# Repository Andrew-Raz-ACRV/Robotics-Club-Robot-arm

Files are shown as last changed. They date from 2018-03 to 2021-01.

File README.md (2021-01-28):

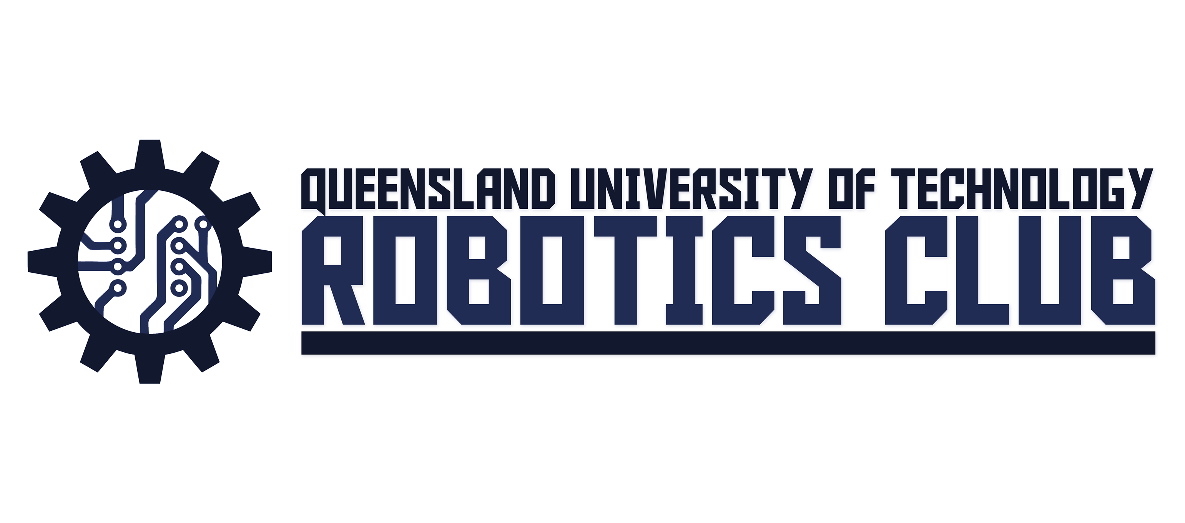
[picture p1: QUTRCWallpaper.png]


# Robotics-Club-Robot-arm
This project is part of the 2018 workshop series for the QUT Robotics club. It is based on the unit called Introduction to Robotics which is a subject focussed on the control of a Robotic arm and the application of computer vision processes. For half the project, the focus was on developing our own brand of robotic arms (Armageddon) with a position-based inverse kinematics controller that made the toolpoint of the robot follow a trajectory given by keyboard presses. The second half expanded the work towards an autonomous picking system where the robot uses a camera to see a ball, given some reference points to its frame of reference, and plan a trajectory to pick up the ball and place it into a box. There is also additional code to teleoperate the arm using a USB gamepad.

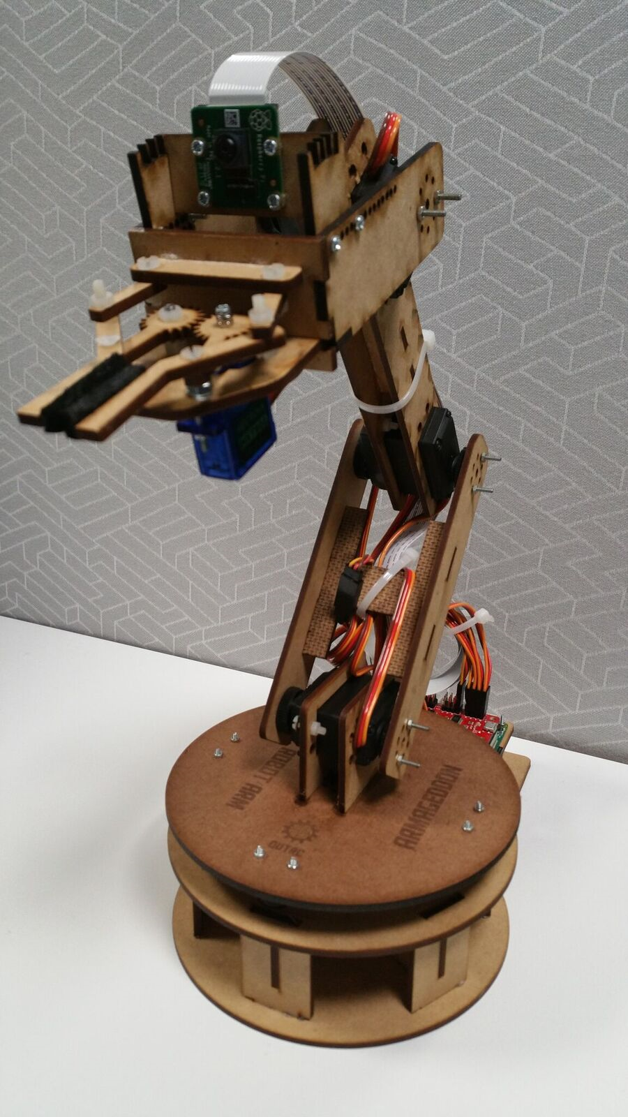
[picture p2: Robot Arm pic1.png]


## Getting Started with the Project
This project is based on using the robotic arms designed by the club which involve components:
* Raspberry Pi 3 B+ with a NOOBS sd card
* Raspberry Pi Camera
* Power adapter for the Raspberry Pi
* Sparkfun Raspberry Pi Servo hat
* Hobby King servos
* Laser cut parts developed by the club which is on this Github
a more comprehensive parts list is in this Github as well.

### Prerequisites
The Raspberry Pi project requires a few installations
- Getch is for capturing keyboard presses: https://pypi.org/project/getch/
- smbus for the i2c communication to the servo hat: https://learn.sparkfun.com/tutorials/pi-servo-hat-hookup-guide/all#software---python
- An old version of opencv that can be installed easily and quickly 
- Optional installation with matlibplot
- Note: you will need to enable i2c and the camera in pi configurations

Installations for the Kinematics Half of the Project:
```
sudo apt-get install getch
sudo apt-get install smbus
```

Installations for the Computer Vision half of the project:
```
sudo apt-get install python opencv
sudo apt-get install python matlibplot
```
USB Gamepad Teleoperation installation:
```
sudo pip install evdev
```
## Running Robot Arm Tests:

Robot Arm Calibration Test:
In Robot Arm control Workshops, you can test the calibration of the servos to see if they are accurate
```
python3 calibration.py
```

Computer Vision Threshold Test:
In Computer_vision_Workshops, you can run a script to see the thresholding
```
python test_video_blobdetection.py
```

In Gamepad demo Test:
Use the first line of code to determine which event the gamepad is (event3 by default)
```
ls /dev/input
python gamepad_demo.py
```
## Contents on this Github:
This Github holds the following:
* Laser cut file (CorelDraw) of the Robot Arm
* Parts List for Constructing the Robot Arm
* MATLAB simulation of the inverse Kinematics provided with Andrew's Kinematics functions
  Run the file RobotArmSimulator.m
* Workshop Slides with Theory explained in them
* Python scripts of the Workshop tasks
* Python scripts of the Final Demo Scripts

## Final Demo Scripts:

In the Terminal, you can run these commands to run the demos:

The Robot Arm Teleoperation Script in Python 3
In Teleoperation_Demo_Python3:
```
python3 RobotArmRaspberryPi_Complete_Code.py
```

The Robotic Vision Autonomous Picking Script in Python 2
In VisionArm_Demo_Python2:
```
python VisionArm.py
```

USB Gamepad teleoperation demo of Robot arm in Python 2
```
python RobotArm_Gamepad_teleop.py
```

## Author

* **Andrew Razjigaev** - *President of the QUT Robotics Club 2018*  

## Acknowledgments
* Student Clubs and Projects (SCAP) Fund 2018
* Krishan Rana - For his Development of the gripper and Laser cut pieces for the joints.
* Marty - For his assistance with running the Computer Vision task

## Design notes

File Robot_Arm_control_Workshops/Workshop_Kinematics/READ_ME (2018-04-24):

Today's Workshop you need to complete a few functions:
In the Utilities module complete:

-Initialise_Robot_arm
-move_arm_deg
-move_arm_rad

In the Kinematics Module Complete:
-ForwardKinematics
Fill in the DH parameters

*You'll need to read the Kinematics document in internet 
Chromium to understand what to fill in ForwardKinematics
Otherwise, just ask and I'll be happy to explain.

After that you can control the arm to go to any 
motor angle you like just for fun in Robot_script.py

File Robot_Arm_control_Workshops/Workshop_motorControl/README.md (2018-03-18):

- Software - Python -
We’ll go over in some detail here how to access and use the pi servo hat in Python.

References: https://learn.sparkfun.com/tutorials/pi-servo-hat-hookup-guide#software---python

- Set Up Access to SMBus Resources - 

First point: in most OS level interactions, the I2C bus is referred to as SMBus. 
If doing this for the first time, you'll need to go to the pi-config settings and enable i2c communication.
Do this by going to the terminal or using the start menu option:

sudo raspi-config

From the window that appears, navigate to 'Interfacing options' which leads to the option of enabling i2c.
The change requires rebooting. Afterwards, you can get the SMBus module by typing this in the terminal:

sudo apt-get install python3-smbus i2c-tools

You can also type in this command to find the part's address which is 0x40 by default:
i2cdetect –y 1 

- Using the SMBus Resources for Motor Control -

Open a python3 script and start typing this code:

import smbus
bus = smbus.SMBus(1)

This imports the smbus module, creates an object of type SMBus, and attaches it to bus “1” of the Pi’s various SMBuses.
We have to tell the program the part’s address. By default, it is 0x40, so set a variable to that for later use.

addr = 0x40

Next, we want to enable the PWM chip and tell it to automatically increment addresses after a write (that lets us do single-operation multi-byte writes).

bus.write_byte_data(addr, 0, 0x20)
bus.write_byte_data(addr, 0xfe, 0x1e)

- Write Values to the PWM Registers to Control Servos -

That’s all the setup that needs to be done. From here on out, we can write data to the PWM chip and expect to have it respond. Here’s an example.

bus.write_word_data(addr, 0x06, 0)
bus.write_word_data(addr, 0x08, 1250)

The first write is to the “start time” register for channel 0. By default, the PWM frequency of the chip is 200Hz, or one pulse every 5ms. The start time register determines when the pulse goes high in the 5ms cycle. All channels are synchronized to that cycle. Generally, this should be written to 0. The second write is to the “stop time” register, and it controls when the pulse should go low. The range for this value is from 0 to 4095, and each count represents one slice of that 5ms period (5ms/4095), or about 1.2us. Thus, the value of 1250 written above represents about 1.5ms of high time per 5ms period.

Servo motors get their control signal from that pulse width. Generally speaking, a pulse width of 1.5ms yields a “neutral” position, halfway between the extremes of the motor’s range. 1.0ms yields approximately 90 degrees off center, and 2.0ms yields -90 degrees off center. In practice, those values may be slightly more or less than 90 degrees, and the motor may be capable of slightly more or less than 90 degrees of motion in either direction.

To address other channels, simply increase the address of the two registers above by 4. Thus, start time for channel 1 is 0x0A, for channel 2 is 0x0E, channel 3 is 0x12, etc. and stop time address for channel 1 is 0x0C, for channel 2 is 0x10, channel 3 is 0x14, etc. See the table below.

Channel #
Start Address
Stop Address

Ch 0
0x06
0x08

Ch 1
0x0A
0x0C

Ch 2
0x0E
0x10

Ch 3
0x12
0x14

Ch 4
0x16
0x18

Ch 5
0x1A
0x1C

Ch 6
0x1E
0x20

Ch 7
0x22
0x24

Ch 8
0x26
0x28

Ch 9
0x2A
0x2C

Ch 10
0x2E
0x30

Ch 11
0x32
0x34

Ch 12
0x36
0x38

Ch 13
0x3A
0x3C

Ch 14
0x3E
0x40

Ch 15
0x42
0x44

If you write a 0 to the start address, every degree of offset from 90 degrees requires 4.6 counts written to the stop address. In other words, multiply the number of degrees offset from neutral you wish to achieve by 4.6, then either add or subtract that result from 1250, depending on the direction of motion you wish. For example, a 45 degree offset from center would be 207 (45x4.6) counts either more or less than 1250, depending upon the direction you desire the motion to be in.

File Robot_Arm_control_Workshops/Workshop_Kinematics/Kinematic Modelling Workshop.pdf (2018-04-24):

KINEMATIC MODELLING WORKSHOP The next two sections refer to Peter Corke’s Textbook [1]. His content is also available as

videos in the Robot Academy website: https://robotacademy.net.au/

Understanding 3D space using Homogeneous Transforms
In robotics, we tend represent the world as a 3D Cartesian space where points are coordinate vectors with components on each axis:

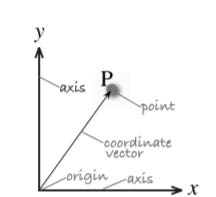
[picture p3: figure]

# PPAA = [TTxx TTyy TTzz]

Each point in space is measured from a Cartesian coordinate frame and has a letter on top that tells you what frame it’s measured from.
A similar set-up is done when you have multiple coordinate frames. A transform from one frame to another is represented as a pose (position and orientation). The letter at the top left of it tells you the frame it’s measuring from and the bottom right letter tells you where the transform goes to:

ξξBB

# AA = tttttttttttttttttt ff AA tttt ff BB

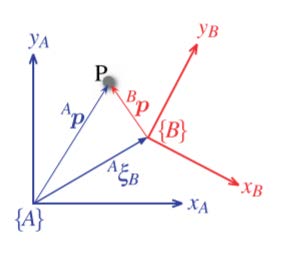
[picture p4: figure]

This is useful when you want to find where one measured point is to another frame e.g.:

# PPAA = ξξBB

# AA PPBB

This means that the transform from frame A to B of the point measured in frame B becomes the same point measured in frame A. This transform can be cascaded to transform from many more coordinate frames:

# PPAA = ξξBB

# AA ξξCC

# BB PPCC

For the robot arm project we’ll use this theory to find where the gripper is from the base:

# PPGGGGGGGGGGGGGG

# BBBBBB = ξξJJJJ JJJJ1

BBBBBB | ξξJJJJ JJJJ2 JJJJ JJJJ1 | ξξJJJJ JJJJ3 JJJJ JJJJ2 | PPGGGGGGGGGGGGGG JJJJ JJJJ3

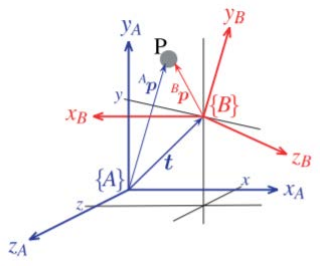
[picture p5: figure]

We can represent the transform as a matrix, like so:
ξξBB

# AA → TTBB

AA =

# | TTxx … RRBB

# AA … TTyy

# | TTzz

0 0 0 1

The matrix is 4 by 4 with the top left 3 by 3 being a 3D rotation Matrix and the forth column having the translational components tt = [TTxx TTyy TTzz] of the transform in each axis. The bottom row is what makes it possible to

use the transforms in this way:

# TTGGGGGGGGGGGGGG

# BBBBBB = TTJJJJ JJJJ1

# BBBBBB × TTJJJJ JJJJ2 JJJJ JJJJ1 × TTJJJJ JJJJ3 JJJJ JJJJ2 × TTGGGGGGGGGGGGGG JJJJ JJJJ3

Where you can use matrix multiplication (dot product) to cascade the transforms. To understand the rotation matrix think of it as an array of
components of each axis. Note: every axis is a unit vector. Based
on the figure to the right, you’ll see that new axis is split into
components measured on the old axis:
RRBB

VV →

∗

# aa aa xxVV aa aa yyVV aa aa zzVV

# xxBB yyBB zzBB

# cos θθ − sin θθ 0 sin θθ cos θθ 0

0 0 1

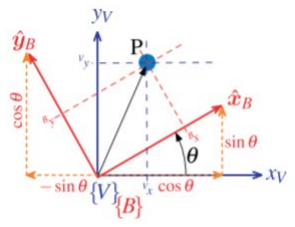
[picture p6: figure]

The matrix means that for some x distance along xxBB is measured as that times cos θθ along

xxVV
And that for some y distance along yyBB is measured as that times − sin θθ along xxVV

And so on for each 3 components on each of the 3 axes … note that the z-axis in the figure is unchanged as theta rotates the frame about the z-axis, so therefore the z-axes components ‘resemble’ the identity matrix. A rotation matrix with no
rotation is an identity matrix. All rotation matrix components
must range between -1 and 1 and the determinant is always 1 to
be a valid rotation matrix. A point can be rotated using matrix multiplication like this:

# PPVV = RRBB

# VV PPBB

# PPVV =

# cos θθ − sin θθ 0 sin θθ cos θθ 0

0 0 1

TTXX
BB
TTYY
BB
TTZZ
BB

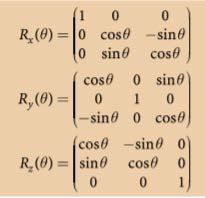
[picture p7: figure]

Rotation in 3D space means that a transform can not only translate in the x, y and z directions but rotate about the x, y and z axes. 3D rotation is commonly described by Euler angles roll pitch yaw. Rotation about the x-axis is roll, rotation about the y-axis is pitch and rotation about the z-axis is yaw.

# RR = RRXX(θθ rrrr) × RRYYθθ ppℎ × RRZZθθyy yy

Putting this together a transformation matrix is used like this:

Let’s say that RRBB

AA is z-axis rotation: RRZZ(θθ) and translation vector is tt = [5, 10, −5]

# PPAA = TTBB

# AA PPBB

# PPAA =

# cos θθ − sin θθ 0 5 sin θθ cos θθ 0 10

0 0 1 −5
0 0 0 1

TTXX
BB
TTYY
BB
TTZZ
BB
1

Which transforms the point PPBB to the same point but measured from the A frame

So overall, in 3D space, any object with a
coordinate frame can be represented as a
transform matrix from the world coordinate frame to it. The matrix consists of a 3 by 3 rotation matrix consisting of 3 parameters and a 3 by 1 translation vector consisting of 3 parameters. A transform is translation and rotation of an object in space based on 6 parameters: x, y, z, roll, pitch and yaw

DH Parameters in the Transform Matrix

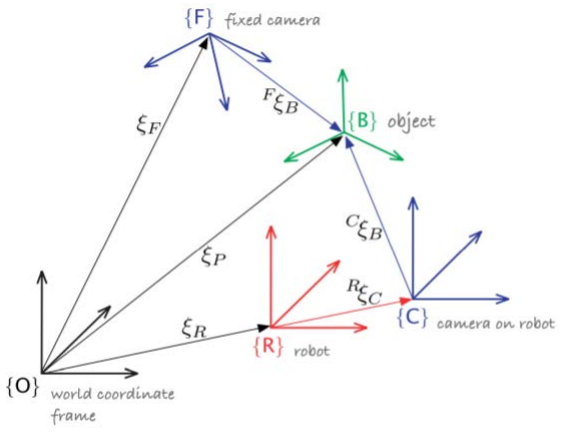
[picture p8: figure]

In the previous section, the transform from one coordinate frame to another in 3D space is described by 6 parameters. Denavit and Hartenburg said that for 3D transforms between revolute joints (ones that rotate only in one axis) can be simplified to only need 4 parameters.

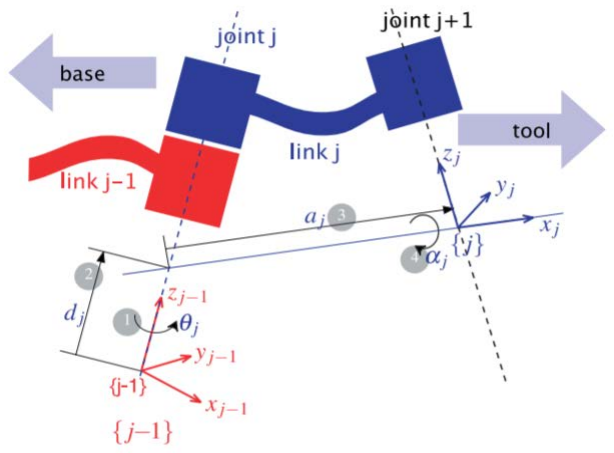
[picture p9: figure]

If you place the coordinate frames in a certain way (mainly placing the z axis as the axis of rotation and the x-axis as an axis to measure between axes), you can have the transform represented by only rotations and translations about the x and z axes:

So from frame j-1 to frame j, the transform is described by parameters θθ, dd, , αα

This yields a standard transformation matrix that we can plug and use for every joint:

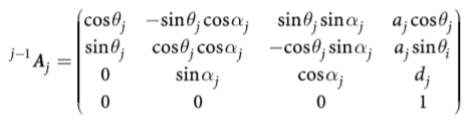
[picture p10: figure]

So every time you want to compute the transformation matrix among the joints, you need to find 4 parameters:

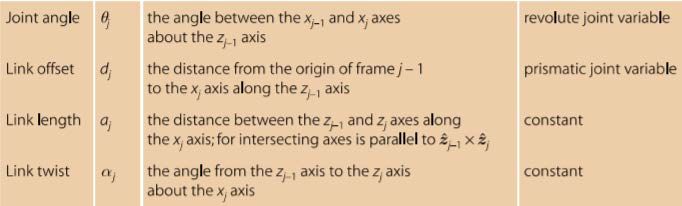
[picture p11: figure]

Solving the Forward Kinematics
Forward kinematics is the problem of finding out where the gripper is from the base of the robot. It can be represented as a function K of joint values to gripper pose:

# xx = KK(qq)

Where x is the tool point pose vector and q is the joint values vector of the robot arm Finding the pose of the gripper from the base can be solved using the transformation matrices learnt before:

# TTGGGGGGGGGGGGGG

# BBBBBB = TTJJJJ JJJJ1

# BBBBBB × TTJJJJ JJJJ2 JJJJ JJJJ1 × TTJJJJ JJJJ3 JJJJ JJJJ2 × TTGGGGGGGGGGGGGG JJJJ JJJJ3

Using the transform matrix TTGGGGGGGGGGGGGG BBBBBB we can extract the overall translation. The next

figure shows how the coordinate frames have been set to find the 4 DH parameters for each joint:

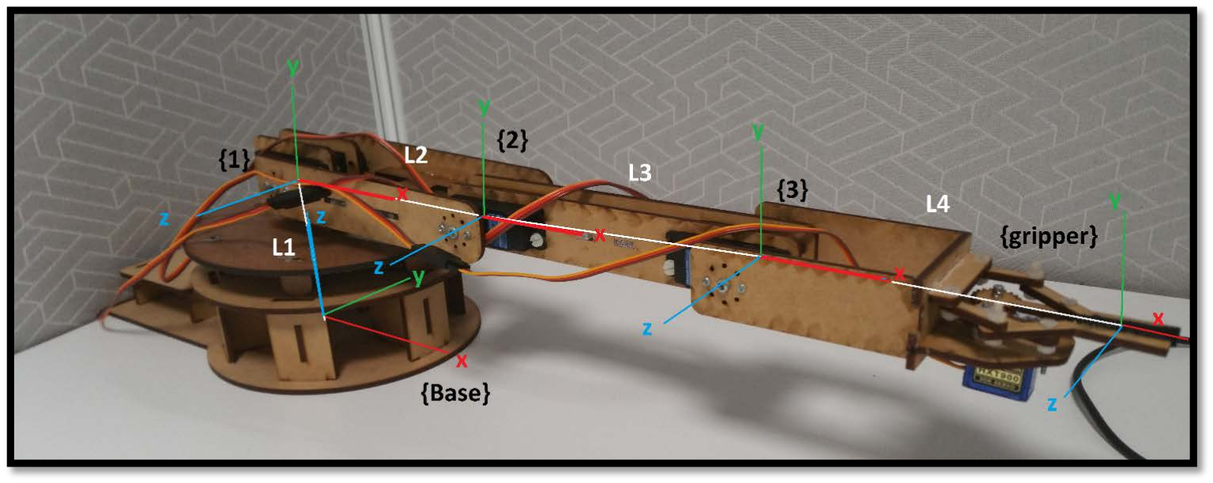
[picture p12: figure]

Note we will need the arm lengths:

# They are: LL1 = 100 , LL2 = 120 , LL3 = 140 , LL4 = 140

All translation is measured in mm
Each joint does a rotation in radians.
The variable angle produced by each joint is

# qq1, qq2, qq3, qq4

Computing the DH parameters yields:

DH Parameters | θθ | dd | aa | αα

# TTJJJJ JJJJ1 BBBBBB

# TTJJJJ JJJJ3 JJJJ JJJJ2

# TTJJJJ JJJJ2 JJJJ JJJJ1 TTGGGGGGGGGGGGGG JJJJ JJJJ3

We find the x, y, z coordinates by extracting the translation vector out of TTGGGGGGGGGGGGGG BBBBBB

The other value that is of interest to know is the pitch angle of the gripper. That value in intuitively going to be the sum of the joints:

# gg aaaa = θθPP = qq2 + qq3 + qq4

As we want to try controlling that angle and the position of the gripper

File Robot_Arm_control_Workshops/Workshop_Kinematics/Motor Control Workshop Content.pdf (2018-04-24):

# Motor Control Workshop Content:

### Low-Level Servo Control

Provided that i2c is enabled in PI-configuration, you may run code that uses the i2c communication which is the SMBus module. To control the servos first import that module and declare a bus connection.
- import smbus
- bus = smbus.SMBus(1)
Then provide the part address for the connection to go to which is 0x40 by default:
- addr = 0x40
Then initialize the settings for the communication by enabling the PWM chip and tell it to automatically increment addresses after a write (that lets us do single-operation multi-byte writes)
- bus.write_byte_data(addr, 0, 0x20)
- bus.write_byte_data(addr, 0xfe, 0x1e)
With this initialized, now the servos can be told to move to certain positions via Pulse Width Modulation (a method of changing the power delivered to a motor by changing the average voltage in the pulses). The yellow cable of the servo connector carries the control signal, used to tell the motor where to go. This control signal is a specific type of pulse train. Servo motors get their control signal from that pulse width. We can write commands to the servo that tell how big that pulse is, for example:
- bus.write_word_data(addr, 0x06, 0)
- bus.write_word_data(addr, 0x08, 1250)

The first write is to the “start time” register for channel 0 (indicated by using 0x06). By default, the PWM frequency of the chip is 200Hz, or one pulse every 5ms. The start time register determines when the pulse goes high in the 5ms cycle. All channels are synchronized to that cycle. Generally, this should be written to 0 i.e. the start of the period should be high. This only needs to be done once.
The second write is to the “stop time” register, and it controls when the pulse should go low (indicated by using 0x08 for channel 0). The range for this value is from 0 to 4095, and each count represents one slice of that 5ms period (5ms/4095), or about 1.2us. Thus, the value of 1250 written above represents about 1.5ms of high time per 5ms period.
Generally speaking, a pulse width of 1.5ms yields a “neutral” position, halfway between the extremes of the motor’s range. 1.0ms yields approximately 45 degrees off center, and 2.0ms yields -45 degrees off center. In practice, those values may be slightly more or less than 45 degrees, and the motor may be capable of slightly more or less than 45 degrees of motion in either direction.
Common servos rotate over a range of 90° as the pulses vary between 1 and 2ms – they should be at the center of their mechanical range when the pulse is 1.5ms: https://learn.sparkfun.com/tutorials/hobby-servo-tutorial#servo-motor-background

To achieve 1ms pulses, use a stop time of 836, likewise, to get 2ms pulses use a stop time of 1664.

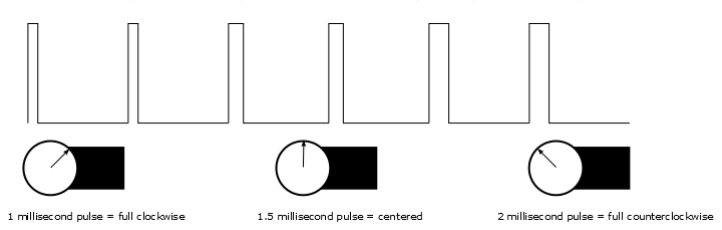
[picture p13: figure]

Using the module time to pause the code so that the servo has time to adjust to its position:
- time.sleep(2) # pause for two seconds
- bus.write_word_data(addr, 0x08, 836) # chl 0 end time = 1.0ms
- time.sleep(2)
- bus.write_word_data(addr, 0x08, 1664) # chl 0 end time = 2.0ms
Essentially, the servo position is controlled by the stop time of the pulse of the PWM which is a value that ranges from 0 (no power) to 4095 (Full power). Keeping it safe, the range used is from 836 to 1664 which allows a good 90 degrees of movement (acceptable for the arm to pick and place objects in its specific workspace).
See Appendix A for the start and stop addresses for using other channels on the PI hat.
For channel 0 in the example, the start address is 0x06 and the stop address is 0x08.

### High Level Control

The low level control showed that the position of the servo can by controlled by PWM pulses governed by integers from the range of 0 to 4095 with a mechanical working range of 836 to 1664. For the interest of understanding the kinematics of the arm, it is necessary to map that PWM to physical degrees or radians of rotation. For that, calibration is done where one should measure the angle output from each joint that undergoes the PWM values of 836, 1250 and 1664. The relationship is proportional and hence a linear relationship is required to map PWM to angle output. Using the calibration data, one can model the servo as a class object in python that has variables like joint limits and functions that can move the servo to a certain degrees or radians or read the current position of the joint. The functions for the PI servo class is in the Robotarm_ServoModule.py file in the workshop folder.

Measuring Convention of the Joints of the Arm:

To measure the joints consistently for each arm, the standard for placing the origin for the angles is proposed based on the right hand rule about the axis of rotation and the coordinate frames later on. To get the idea, the robot in the picture has the revolute base at 0, the next joint is at 135, the joint above that is at -100 and the joint above that one is at -90 degrees.

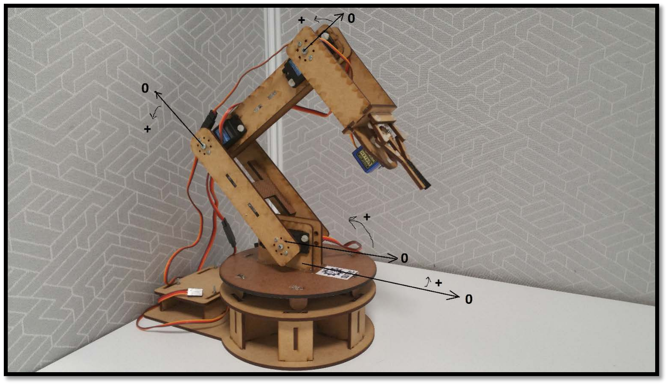
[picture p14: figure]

For the Robot arm, generally channels 0 to 4 are used for the whole arm. An easy pattern to find the addresses is that each hexadecimal increments by 4 for every channel:
Example:
Ch.0 start = 0x06, | Ch.1 start = 0x06 + 4*1 = 0x0A, Ch.2 start = 0x06 + 4*2 = 0x0E
Ch.0 stop = 0x08, | Ch.1 stop = 0x08 + 4*1 = 0x0C, Ch.2 stop = 0x08 + 4*2 = 0x10
Channel # | Start Address | Stop Address
Ch. 0 | 0x06 | 0x08
Ch. 1 | 0x0A | 0x0C
Ch. 2 | 0x0E | 0x10
Ch. 3 | 0x12 | 0x14
Ch. 4 | 0x16 | 0x18
Ch. 5 | 0x1A | 0x1C
Ch. 6 | 0x1E | 0x20
Ch. 7 | 0x22 | 0x24
Ch. 8 | 0x26 | 0x28
Ch. 9 | 0x2A | 0x2C
Ch. 10 | 0x2E | 0x30
Ch. 11 | 0x32 | 0x34
Ch. 12 | 0x36 | 0x38
Ch. 13 | 0x3A | 0x3C
Ch. 14 | 0x3E | 0x40
Ch. 15 | 0x42 | 0x44

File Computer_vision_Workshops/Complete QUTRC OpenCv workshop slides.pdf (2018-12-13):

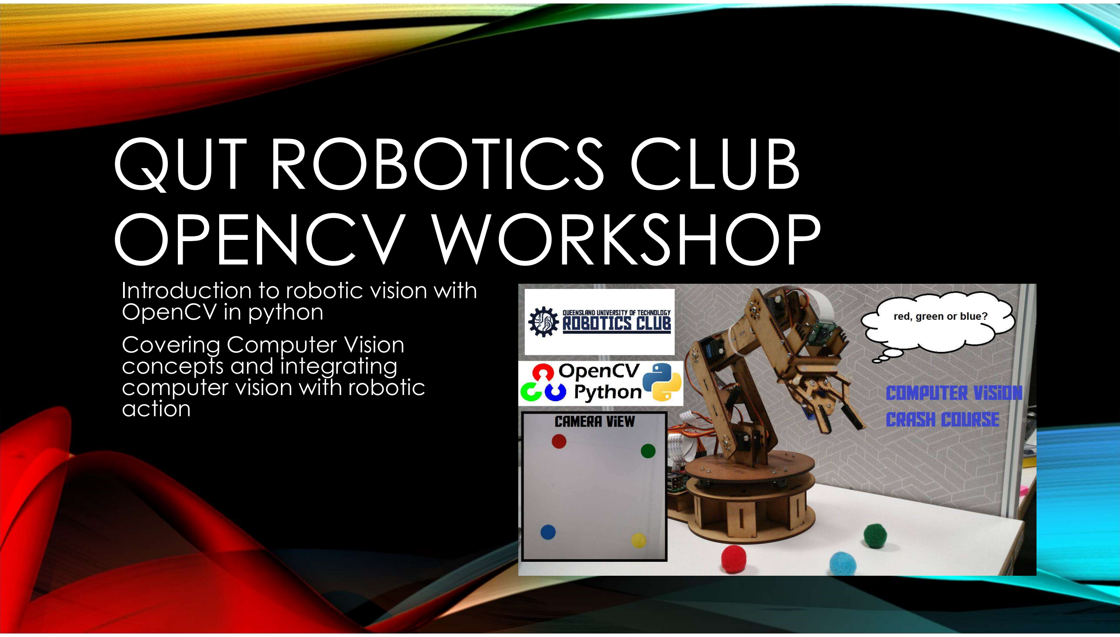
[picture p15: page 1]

# QUT ROBOTICS CLUB OPENCV WORKSHOP

Introduction to robotic vision with
OpenCV in python
Covering Computer Vision concepts and integrating computer vision with robotic

action

# GETTING OPENCV IN PYTHON ON A COMPUTER WITH ANACONDA

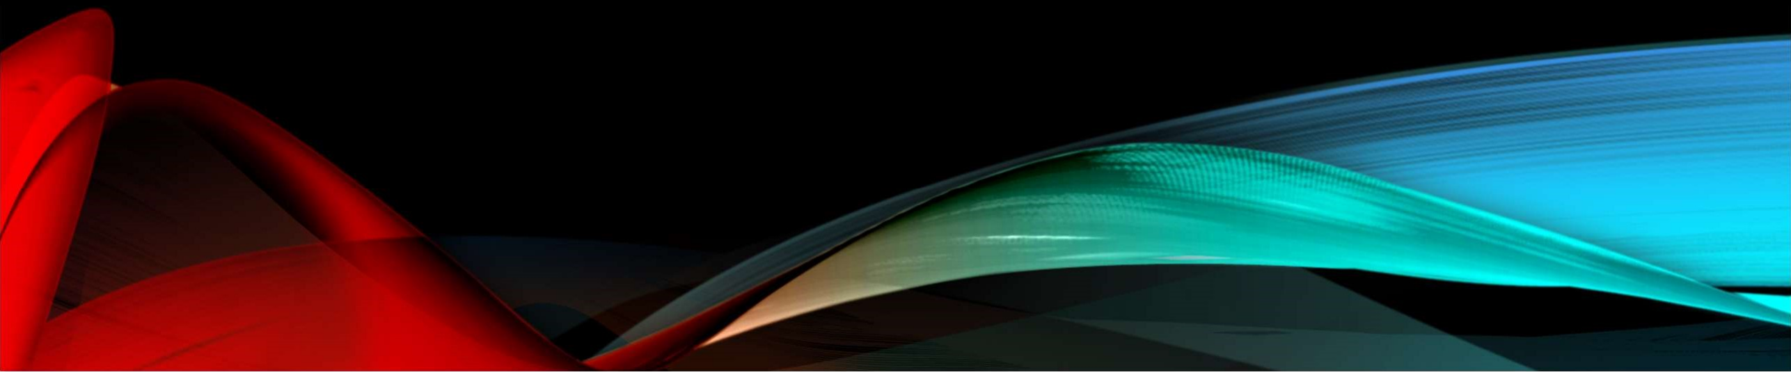
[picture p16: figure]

## INSTALLING OPENCV ONLY FOR PYTHON PRACTICE ON A COMPUTER

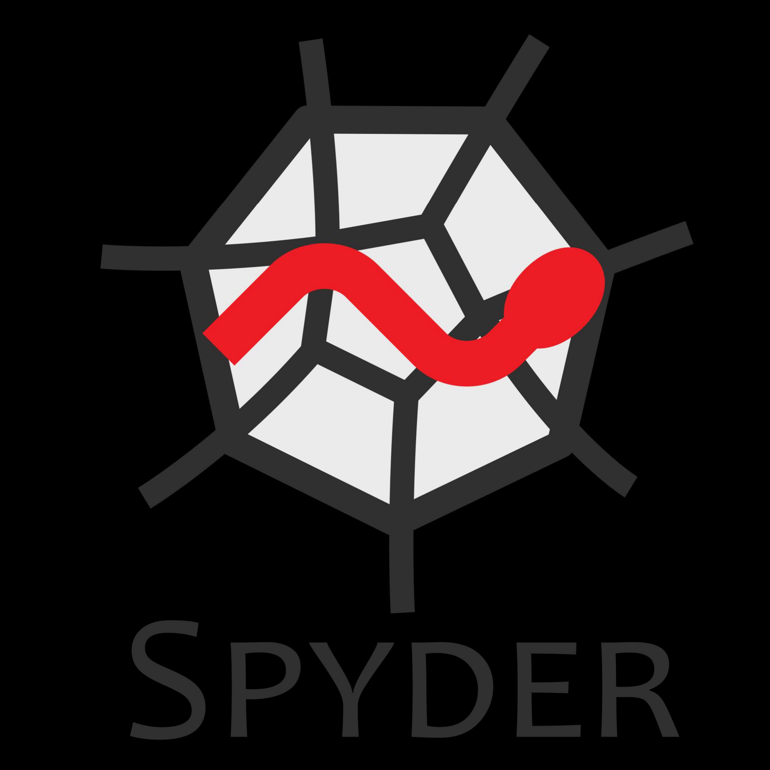
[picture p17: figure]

- Search for Anaconda online to download the Spyder IDE for Python development: Pick Python 2.7 for OpenCV!
- https://www.anaconda.com/download/#windows
- Some University computers may already have this one installed

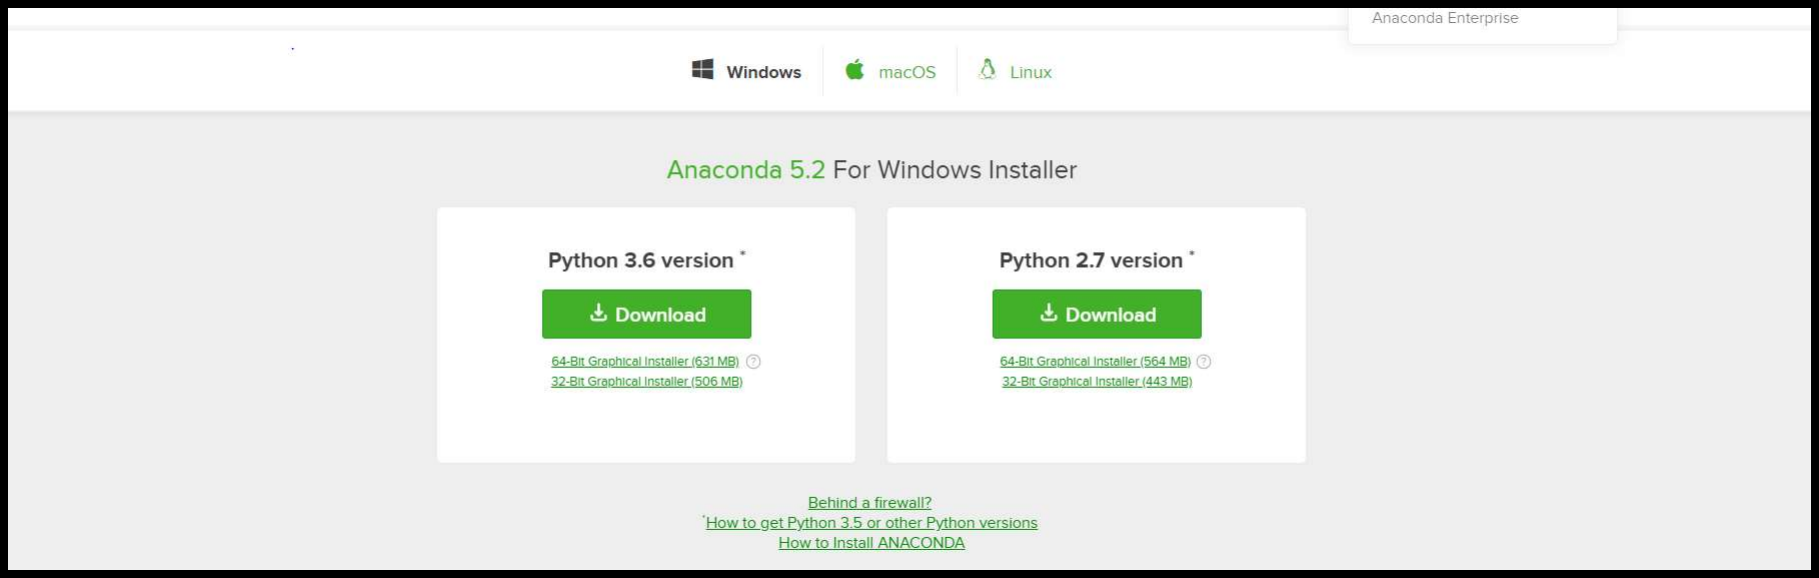
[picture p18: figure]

## INSTALLING OPENCV ONLY FOR PYTHON PRACTICE ON A COMPUTER

- Once you have Python 2.7 working on Spyder, You can go get OpenCV!
- https://opencv.org/releases.html

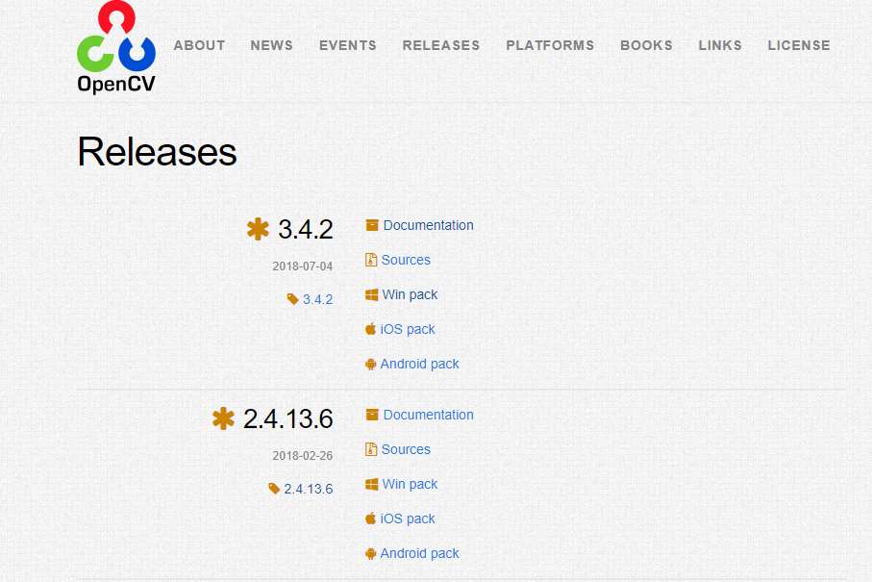
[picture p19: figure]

## INSTALLING OPENCV ONLY FOR PYTHON PRACTICE ON A COMPUTER

- Go find the OpenCV package (cv2.pyd) from the OpenCV you downloaded/ extracted:
- C:\Users\...\Documents\OpenCV\opencv\build\python\2.7\x64
- Copy the file and paste it into the library site-packages for anaconda2 usually its in here:
- C:\Users\...\AppData\Local\Continuum\anaconda2\Lib\site-packages

## INSTALLING OPENCV ONLY FOR PYTHON PRACTICE ON A COMPUTER

- Once you’ve pasted it into site-packages, start up Spyder and in the console you should be able to import cv2
- Notice its important to have the right Python interpreter (Python2.7) using the module or otherwise it may not find it and give an error. Also note that the version stated is the release number on OpenCV’s website.

# IMAGE PROCESSING FOR ROBOTIC VISION

Colour Thesholding

# GREYSCALE IMAGES

- What is an image or a frame? It’s a matrix with colour intensity values:

This is how a grayscale image is DRC back in the old days… structured, it starts at u,v
coordinate (0,0) at the top left
corner. Each coordinate is a pixel

Intensity is usually an Uint8 unsigned integer 8 bit:
(0 to 255) or a float (0 to 1)

# THRESHOLDING GREYSCALE IMAGES TO GET BINARY IMAGES

- Thresholding is a Logic operation, The idea is that we loop each pixel and test if the intensity is greater or less than the threshold value. • If pixel value is greater than threshold -> answer is 1 (white) else it is 0 (black). It can be a range too. This gives us a binary image where each pixel is logical (0 or 1) that’s (white or black)

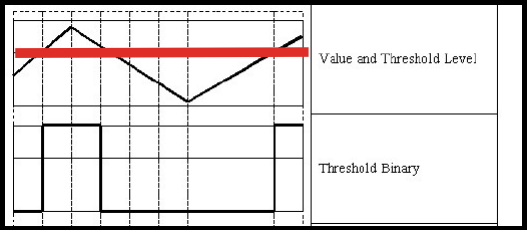
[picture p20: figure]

- Usually We threshold with a range. If pixel value is between a lower threshold and upper threshold, make it

### 1 else make it 0

- cv.threshold(image,lower,upper,cv.THRESH_BINARY)
- https://docs.opencv.org/3.4.0/d7/d4d/tutorial_py_thresh olding.html

# RED GREEN BLUE IMAGES

- A RGB image is a Red Green and Blue channel image.
- Its made of 3 layers of grayscale images. That is size = (width,height,3)
- You can separate them as planes like in the code below, notice that OpenCV structures it as Blue Green Red.
- In Python the first plane starts at 0 then 1 then 2

b, g, r = image[:, :, 0], image[:, :, 1], image[:, :, 2] # For RGB image

# THRESHOLDING IN DIFFERENT COLOUR PLANES

- Since in Colour each pixel is a BGR vector • Pixel = [b , g , r]
- What we do is just do the same type of thresholding but for each colour plane
- Use cv2.inRange(imageBGR7,lower,upper)
- https://medium.com/@ckyrkou/color-thresholding-in-opencv-91049607b06d

# HSV COLOUR SPACE

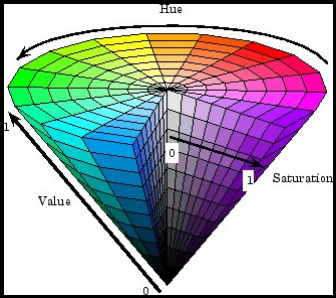
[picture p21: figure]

- RGB is a simple colour space suitable to storage and computing etc.
- But that colour maybe unintuitive to threshold or interpret for the Human eye. It may also be prone to brightness/darkness problems
- This is why there exists another Colour space called HSV (Hue Saturation and Value)
- HSV is designed to be more like a colour wheel where you only need to vary the Hue value to get the colour you want from the rainbow.

# HSV COLOUR SPACE

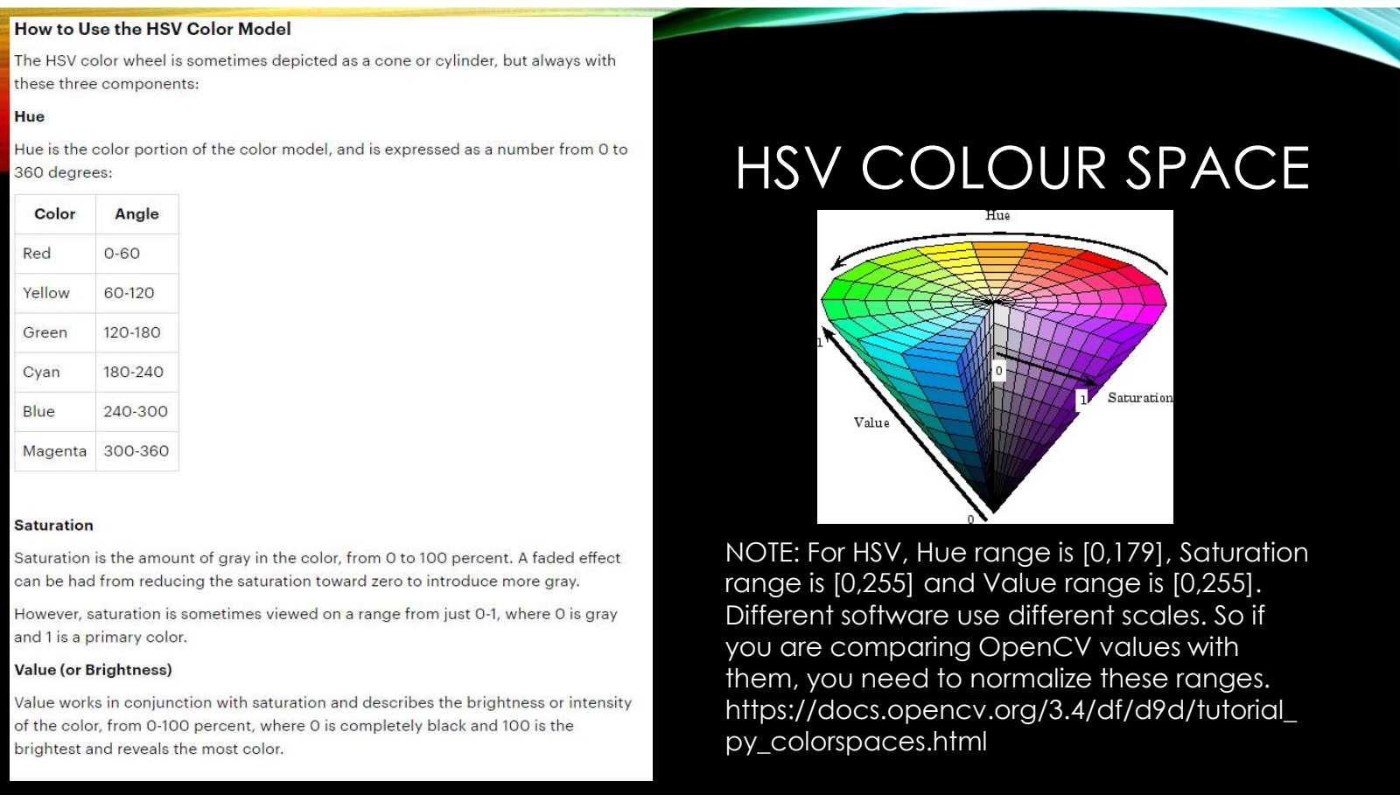
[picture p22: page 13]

NOTE: For HSV, Hue range is [0,179], Saturation range is [0,255] and Value range is [0,255]. Different software use different scales. So if you are comparing OpenCV values with them, you need to normalize these ranges. https://docs.opencv.org/3.4/df/d9d/tutorial_py_colorspaces.html

# THRESHOLDING IN HSV EXAMPLE

- First convert BGR to HSV
- hsv = cv2.cvtColor(image, cv2.COLOR_BGR2HSV)
- Then Do the inRange function with the HSV values
- #Threshold bounds note its (h,s,v) so 100<h<140, 50<s<255, 50<v<255
- #Note Hue range is [0,179], Saturation range is [0,255] and Value range is [0,255]
- lower_bounds = np.array([100,50,50])
- upper_bounds = np.array([140,255,255])
- mask = cv2.inRange(hsv,lower_bounds,upper_bounds)
- https://docs.opencv.org/3.4/df/d9d/tutorial_py_colorsp aces.html

- But there also a | RGB - CHROMATICITY

technique to fix the
brightness problem
- The solution is to make
each colour relative the
overall brightness of the
image
- sum the r,g,b matrices
and divide each colour
matrix by that sum:
- The image becomes a
float from 0 to 1

# THRESHOLDING IN CHROMATICITY EXAMPLE

- To do chromaticity you may need to do things the old fashioned way, that’s write a for loop to go around each pixel and compute the chromaticity
- http://answers.opencv.org/question/54727/convert-rgb-brg-to-rg-chromaticity/

# TASK FOR THE WORKSHOP

- You’re Task is to threshold a variety of images (or your own) from the arm project to images I retained from older subjects. I also found a DRC 2016 image.

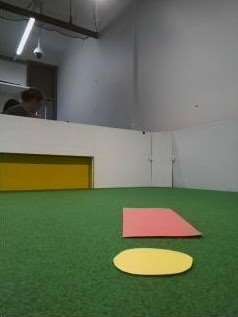
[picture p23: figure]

# NEXT WEEK’S OBJECTIVES

- Masks and morphological image processing with Binary images
- Edge Detection from Binary images
- Blob detection with binary images
- Extracting Features about blobs

# EXTRACTING FEATURES FOR ROBOTIC VISION

Blob detection from Binary Images

# CONTINUING FROM LAST WEEK…

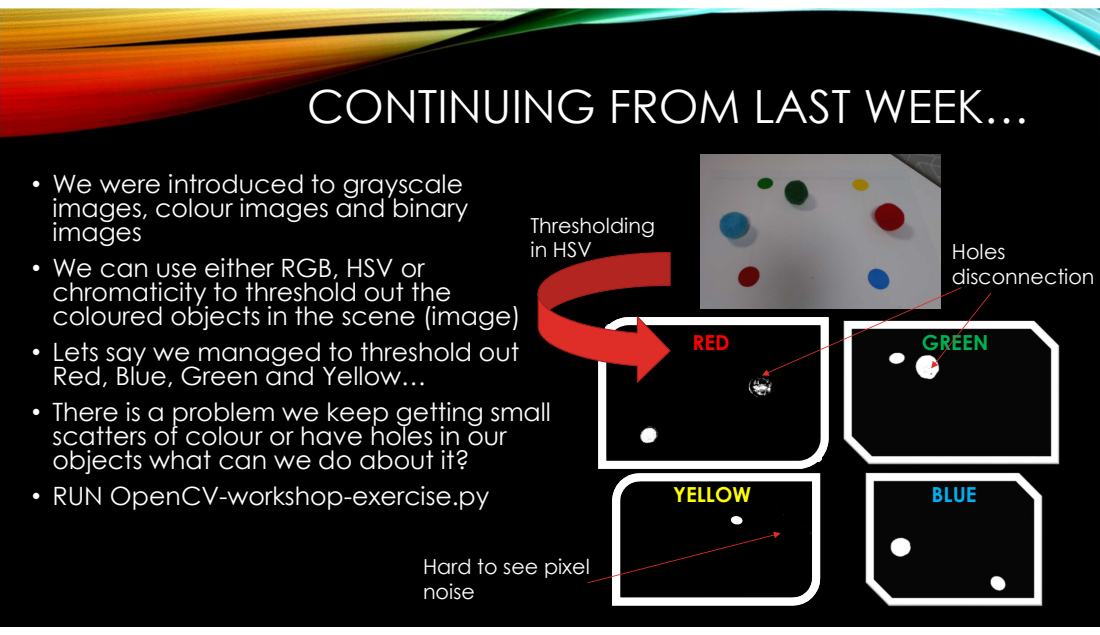
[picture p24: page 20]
RED; GREEN; YELLOW; BLUE; Holes disconnection; Thresholding in HSV

• We were introduced to grayscale
images, colour images and binary
images
• We can use either RGB, HSV or
chromaticity to threshold out the
coloured objects in the scene (image)
• Lets say we managed to threshold out
Red, Blue, Green and Yellow…
• There is a problem we keep getting small scatters of colour or have holes in our
objects what can we do about it?
• RUN OpenCV-workshop-exercise.py

Hard to see pixel
noise

## MORPHOLOGICAL IMAGE PROCESSING: A SPATIAL OPERATION

- Morphological image
processing can be the answer. • We use a spatial operation

where each pixel becomes a function of the pixels in the window (or also called a kernel or a structuring element)
- Morphological Image
processing is the case where we apply LOGIC Kernal
functions in BINARY images. • https://docs.opencv.org/3.0-

beta/doc/py_tutorials/py_imgp roc/py_morphological_ops/py_ morphological_ops.html

# DILATION: MORPHOLOGICAL

# PROCESS

- For each pixel, the kernel does an OR operation. That means if ANY value in the pixel region (like the 3x3 kernel in the figure) is 1 then the result is 1 else its 0.
- This has the effect of making white thresholds bigger

# EROSION: MORHOLOGICAL PROCESS

- For each pixel, the kernel does an AND operation. That means if ALL

values in the pixel region (like the 3x3 kernel in the figure) is 1 then the result is 1 else its 0.
- This has the effect of shrinking white thresholds and removing any group of pixels smaller than the kernel.

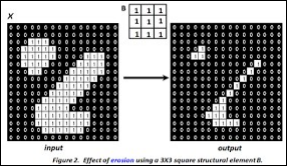
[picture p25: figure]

# OPENING AND CLOSING

- We can use these processes to remove thresholding noise and fill in gaps our thresholding failed to do…
- Opening does Erosion first then Dilation. This kills small noise and retains the shape of the big thresholds.
- Closing does Dilation first then Erosion. This partially fills in gaps and holes in the thresholds while retaining the shape we want.

# GETTING AN EDGE OR BOUNDARY WITH A DIADIC PROCESS

- We can also use dilation and erosion to get an outline of a shape.
- We do this by first dilation in I1 and erosion in I2, we then do subtraction I1 – I2 to get an image with the outline:

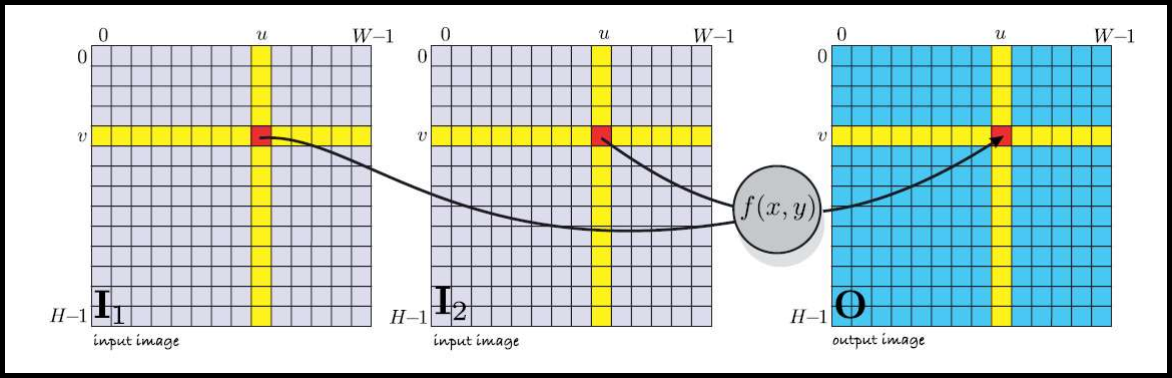
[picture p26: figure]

# DOING THIS IN OPENCV:

- Kernel initialisation: kernel = np.ones((5,5),np.uint8) #Gives a 5x5 kernel
- Dilation: | dilation = cv2.dilate(img,kernel,iterations = 1)
- Erosions: | erosion = cv2.erode(img,kernel,iterations = 1)
- Opening: opening = cv2.morphologyEx(img, cv2.MORPH_OPEN, kernel)
- Closing: | closing = cv2.morphologyEx(img, cv2.MORPH_CLOSE, kernel)
- Edge: | gradient = cv2.morphologyEx(img, cv2.MORPH_GRADIENT, kernel)

- Now we have a binary image that clearly

‘figuring out where they are in the image’
- The last thing we will cover is how to

# BLOB ALGORITHM:

- We do wants called a connectivity analysis with the image. That is we check which


same value pixels are next to each other. It


can be 4 connectivity or 8 connectivity: where 8 connects diagonally the same pixels. The algorithm outputs a list of keypoints that correspond to the number white threshold ‘blobs’ in the image.


## FEATURE EXTRACTION FROM BLOBS (CENTROID, SHAPE AND AREA)

- From each blob, we can compute the centroid, area, circularity, convexity Inertia etc…
- The centroid is just the average coordinate point:
- Circularity tells you how circular the shape is from 0 to 1
- This is a powerful tool to recognise shapes,

## FEATURE EXTRACTION FROM BLOBS (CENTROID, SHAPE AND AREA)

- Link https://www.learnopencv.com/blob-detection-using-opencv-python-c/
- Here shows some info of blob features you can detect:
- OpenCV can even do Blob detection filtering out the blobs based on features.

#------------------Setting up blob detection------------------------#

# Setup SimpleBlobDetector parameters.

params = cv2.SimpleBlobDetector_Params()

# Change thresholds - accept all white blobs params.minThreshold = 0;

params.maxThreshold = 255;

# Filter by Area.

params.filterByArea = False params.minArea = 1500

# Filter by Circularity

params.filterByCircularity = False params.minCircularity = 0.1

# Filter by Convexity

params.filterByConvexity = False params.minConvexity = 0.87

# Filter by Inertia

params.filterByInertia = False
params.minInertiaRatio = 0.01

# Set up the blob detector with parameters. detector = cv2.SimpleBlobDetector_create(params)

# CODE ADVICE TO BLOB

DETECTION: • # Detect blobs. • red_mask = cv2.bitwise_not(red_mask)

- keypoints = detector.detect(red_mask)
- red_mask = cv2.bitwise_not(red_mask) #Return the colours to normal • #Check no block detection case: • n = len(keypoints)
- if n is 0: • | | | | print('No red blobs detected')
- else: • | | | | #Label the red blobs found
- | for keypoint in keypoints: • | x = keypoint.pt[0] • | y = keypoint.pt[1] • | s = keypoint.size
- cv2.putText(red_mask, 'Big Red Circle', (x,y), cv2.FONT_HERSHEY_SIMPLEX, 2, (255, 255, 255), 2, cv2.LINE_AA)

How we do blob
detection. Note in
OpenCV we need to
invert the colours with
bitwise_not

How we get the
centroid and size from
a blob

In a real system you need to take account of the possibility of there being no blob.

- Find the coordinates of | TASK FOR WORKSHOP:
the 4 sticker dots in
test1.jpg Using Thesholds,
morphological image
processing and blob
detection
- Use the put Text
command to label what
the blob represents
| BLUE
YELLOW | RED

GREEN

## NEXT WEEK’S OBJECTIVES (LAST OPENCV WORKSHOP IN LAB)

- Locating the Position of the balls using Perspective Correction by applying Homography
- Maybe some other topic you guys suggest…
- After Next week and the student break, we will turn the code from these workshops into a ‘vision system’ on the Pi, sampling captured frames from the Pi camera instead of the test images here.

# IMAGES TO ACTION

Methods to take image features to Robot actions

# CONTINUING FROM LAST WEEK


• We used morphological
image processing to fix
thresholding defects.
• We used blob detection to
extract features such as the
centroid of the stickers in the
image.
• The Problem is that now we
want to figure out how to use
that data as an input for
robot actions our robot

# ROBOT ARM PICKING PROBLEM


- We want to turn the image features we detected previously into coordinates for picking up the balls. • There are a mainly 2 methods we can apply: • Reactive –at every iteration, the robot sees and moves. (usually better in dynamic scenarios can be simple or complex)
- Planning – Determine a path for the robot to go to based on the image data collected. (does a lot of computation

initially and then executes the whole action this can be easier to deal with sometimes)

# REACTIVE EXAMPLE: POTENTIAL FIELD IN SOCCERBOTS


- In Mechatronics Design Project 2, you guys would do a soccerbot project. • What potential field does is that using the detected objects, you make a certain direction more attractive or repulsive

than other directions. • E.g. the orange ball has high attractiveness and the black obstacle

has repulsiveness. When the goal is in your possession, the yellow or blue goal has high attraction

- The robot will turn towards the area with high attractiveness and move in that direction until the next state in execution

# REACTIVE EXAMPLE IN DROID RACING CHALLENGE

- This can be used in DRC too!
- The droids is repulsed from the yellow and blue lanes, the purple obstacle and the other red vehicles (or attraction if you want to knock out
the competition he he he…)
- Its all a matter of how you control the gains for robot motion that’s steering and velocity for a mobile robot
- The robot steers until it gets the desired direction i.e. the most
attractive path is in the middle pixel coordinate ->

# REACTIVE CONTROL FOR ROBOT ARM

- For a robot arm, you can do a similar thing. The robot can face the scene and measure the error in
image feature position | with
reference to the position where the gripper can pick it up. • The error goes as a gain to
increment the position using updates of | . • You can also use area of the blob
as a limit to how much | you do
- You just need to know how image feature error changes as the camera moves so that the error

converges
- This is easier to think of it in a simple trajectory (like moving downwards). This is basic ‘visual servoing’ but it is a lot trickier when you need to rotate the camera too…

# PROS AND CONS OF REACTIVE MODEL

- Pros: • Simple control system that can be fast • Has Feedback and Reacts to dynamic changes in the environment • Cons
- Does image processing each step so the speed is at the mercy of the computation time for each iteration. • Be careful what happens in-between iterations it could be that it misses something

and gets stuck. • Sometimes hard to formulate a controller for the problem

- Attraction and repulsion can cancel each other out making your robot stuck

# PLANNING EXAMPLE: GENERATING A MAP AND USING IT

- Sometimes it may be easier to plan the trajectory rather than reacting to it. Lets say we recorded a map of the

environment (like recording the maze paths after some initial line following) we can then plan a motion towards the goal. • E.g. in Mech Project 1: the line follower, you can record the path using a reactive method and then execute a fast planned

trajectory afterwards
- E.g. in Advanced Robotics: We generate a map using SLAM (simultaneous Localisation and mapping). We then plan

how to move to the place to send rescue supplies

# PLANNING EXAMPLE: GRAPH SEARCH

- In a maze you can use an AI search algorithm to move to a target around some obstacles to reach the end. But this is getting off topic…
- This is some AI applications which involve path planning. You may find A* a popular search algorithm find out more here: https://www.redblobgames.com/pathfinding/a-star/introduction.html

# PLANNING EXAMPLE: LOCATING THE BEACONS TO MAKE THE MAP

- What’s the main challenge in planning? That’s probably locating where everything is accurately
- In Advanced Robotics you need to estimate where the beacons are from the camera i.e. range and bearing, to put onto a map your building
- There is no formal method given in the subject but there are a few simple methods people think of or are suggested by tutors in the subject. • A simple method is to map an function

that relates the distance to the object with something like the area of the blob.

# PLANNING EXAMPLE: LOCATING THE BEACONS TO MAKE THE MAP

# PROS AND CONS IN PLANNING

- Pros:
- Does motion swiftly by putting all the hard computations in the planning part
- Can be easier to design a state machine program with it as it separates the parts
- Can plan optimal paths
- Cons:
- Realises on the approximation of mapping/locating objects in the environment. Poor estimation gives ‘open loop’ fails like missing the target completely
- Fails in Unstructured and dynamic environments unless prior assumptions are done

# PLANNING IN THE ROBOT ARM

- We can use the camera to estimate where the objects are in the robot’s reference frame.
- This may involve determining where the object is in reference to the camera or to predefined objects in the robot space.
- For our task we will be given the position of the four stickers and we will determine where the objects are with reference to them.
- To complete this we will use homography

# HOMOGRAPHY: FROM TABLE TO TASK SPACE

- Homography is a transformation from one image or plane to another. With it we can do things like make that cathedral looking face on rather than at that angle
- To do this we need at least 4 points that relate the two images to solve the transformation matrix. Note the 3rd value is a scale of the x,y coordinate which should be normalised to 1

# THIS IS DONE IN INTRO TO ROBOTICS BUT IN MATLAB

- Code in OPENCV Python
- #The 4 small points from source image
- pts_src = np.array([red_dot, yellow_dot, green_dot, blue_dot])
- #Coordinates in actual cartesian space where 1 is a scale term
- pts_dst = np.array([[175, 50, 1],[275, -50, 1],[275, 50, 1],[175, -50, 1]]) #yaxis 50,-50
- # Calculate Homography
- h, status = cv2.findHomography(pts_src, pts_dst) #h is the transform from that image to that
- # Warp source image to destination based on homography
- im_homography = cv2.warpPerspective(imageBGR, h, (300,250))
- #Find coordinate of target by matrix multiplication:
- pts_target = np.array([x,y,1])
- coordinate = np.dot(h,pts_target)

# HOMOGRAPHY IN OPENCV FOR OUR APPLICATION


- We know where the 4 stickers are located at positions relative to the base of the robot arm.
- Since we have coordinates of the 4 stickers from the camera blob detection, we can find the transform and use it to locate the picking targets.
- E.g:
https://www.learnopencv.com/homography-examples- usingopencvpython-c/

• Using the centroids of the 4 stickers,; TASK FOR WORKSHOP

determine the Homography transform to
find 3D position of the location of the
picking targets
• Note: the balls have a diameter of 2cm
• Hint you may need to normalise the image
coordinate (u,v,w) -> (u/w, v/w, 1)

# ADDITIONAL CONTENT FOR OPENCV WORKSHOPS

Content related to this set of OpenCV Workshops

# HOUGH TRANSFORM CIRCLE DETECTION

- We could have used this algorithm instead of blobs as it can find circles in an image:
- https://docs.opencv.org/3.1.0/da/d53/tutorial_py_houghcircles.html

# EDGE DETECTION ALGORITHMS

- There are a few algorithms to find edges including Sobel and canny:
- https://docs.opencv.org/3.1.0/da/d22/tutorial_py_canny.html
- https://docs.opencv.org/3.0- beta/doc/py_tutorials/py_imgproc/py_gradients/py_gradients.html

# OPENCV AND RASPBERRY PI

Installing and using our OpenCV Techniques on the Raspberry PI

# PI CAMERA INSTALLATION


### 1. Attach Pi Camera like so to the Camera Mount: 2. Note to unlock the slot for the ribbon cable when swapping it for the longer

version.

### 3. On the PI, go to configurations

($ sudo raspi-config)

### 4. Go to the option to Enable the Camera, you’ll need to reboot to take that

into effect

### 5. Now you can test the quality of your image. In the terminal run this

command:
$ raspistill –v –hf –vf –o output.jpg

### 6. The –v gives you capture information, -hf and –vf flip the imae in the vertical

and horizontal directions (i.e. corrects the fact that the pi camera is upside down)

### 7. You should have a file output.jpg in the PI folder, if the camera image was

blank, try reconnecting the ribbon cable to ensure the connection works

### 8. Now install the picamera module:

$ pip install "picamera[array]“

### 9. For more details: https://www.pyimagesearch.com/2015/03/30/accessing-

the-raspberry-pi-camera-with-opencv-and-python/

# RASPBERRY PI OPENCV QUICK INSTALL

- You’ll need internet connection… If on campus, set up a mobile hotspot and get the Raspberry Pi connected to it on if installing on campus. • Run these commands in the terminal to install opencv quickly on the PIs
- sudo apt-get python-opencv
- sudo apt-get python-matplotlib (optional but is useful or plotting things)
- This should take some minutes and only require about 100Mb (as far as I remember)
- Once you have completed these, test the installation by opening a Python 2 IDE and running the commands: • import cv2
- cv2.__version__

# CAPTURING FRAMES FROM THE PI CAMERA IN PYTHON

- A frame is an image from a video which is a series of images. On the raspberry Pi we can take a single image or access frames from a video stream.
- https://www.pyimagesearch.com/2015/03/30/accessing-the-raspberry-pi- camera-with-opencv-and-python/

WORKSHOP TASK: • Using the PI camera and all that has been

installed on the PI, do a video stream from the
camera and make it so that it displays the
thresholding for the colour red in real time. • Adjust the thresholding to make this robust.

Make this code reusable so that you can test thresholding quality in different scenarios (this can be useful if lighting conditions change a lot)
- In addition to this, get blob detection running too and see if it can detect whether it’s a small or a big circle. • Python scripts from the previous OpenCV

workshops shall be distributed by USB to the PIs at the workshop.

RED

# SYSTEMS INTEGRATION

- We now have a mechanical system (robot arm) and it has kinematics software
- We also have a vision system (the camera) and the software associated with that
- Now we need to use both systems to solve the automation problem which is to program the robot to see the coloured balls in the task space, pick them up and place them in a box until there are no balls for some time.
- A good structure to figure out how to program the process is to use what's called a Finite state machine. It is simply a diagram of each ‘state’ the robot can be in and what process is done to change from one state to the other
- Have a go at thinking about how you can structure your code for automated pick and place robot arms

# FINITE STATE MACHINE


- For the automated picking task, the robot needs to see the table, move to a ball, grab it successfully, place it in the box and redo until
there are no balls left and it is done waiting for any
more.
- The diagram to the right describes the state machine for the problem
- State machines are simple and generally are suitable for many programming problems

## TASK: COMPLETE THE PROGRAM TO GET THE ROBOT TO PICK UP OBJECTS AUTONOMOUSLY


- Tips: you can use while
loops to represent each
state and if statements to represent the check
condition to escape the
state.
- Examples of other picking machines:

# END OF WORKSHOP SLIDES!

Now its just programming
and debugging!
Good Luck

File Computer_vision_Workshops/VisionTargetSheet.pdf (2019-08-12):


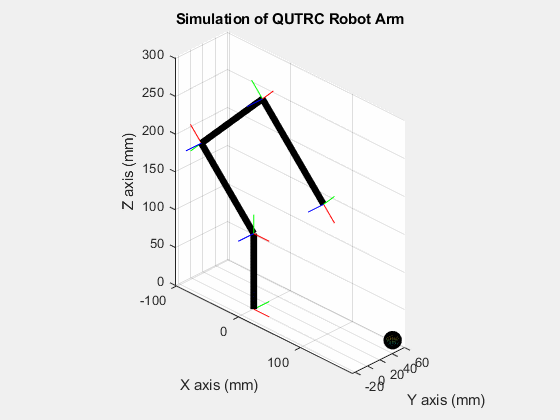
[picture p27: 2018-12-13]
MATLAB Robot Arm Simulation/QUTRC_RobotArm_Simulation.gif

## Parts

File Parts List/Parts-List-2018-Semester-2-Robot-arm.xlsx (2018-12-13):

Parts List for Workshops with the Robot Arms
Robot arm Parts | Exact Quantity for One arm | Function: | Supplier | Website:
Electromechanical components
Turnigy™ TGY-S901D DS/MG Robot Servo 13kg / 0.14sec / 58g | 4 | Joint Actuator | HobbyKing | https://hobbyking.com/en_us/turnigytm-tgy-s901d-ds-mg-robot-servo-13kg-0-14sec-58g.html
HXT900 Micro Servo 1.6kg / 0.12sec / 9g | 1 | Gripper Actuator | HobbyKing | https://hobbyking.com/en_us/hxt900-micro-servo-1-6kg-0-12sec-9g.html
30CM Servo Lead Extention (JR) with hook 26AWG (5pcs/bag) | 1 | Connect distal actuators | HobbyKing | https://hobbyking.com/en_us/30cm-servo-lead-extention-jr-with-hook-26awg-5pcs-bag.html
SparkFun Pi Servo HAT | 1 | Pi Hat for servo control | Sparkfun | https://www.sparkfun.com/products/14328
Raspberry Pi GPIO Tall Header - 2x20 | 1 | Connect Pi to Hat | Sparkfun | https://www.sparkfun.com/products/14017
Raspberry Pi Components
Raspberry Pi Camera Board v2 - 8 Megapixels | 1 | Camera for Robot | Core Electronics | https://core-electronics.com.au/raspberry-pi-camera-board-v2-8-megapixels-38552.html
Flex Cable for Raspberry Pi Camera - 1 meter | 1 | Connect distal Camera | Core Electronics | https://core-electronics.com.au/flex-cable-for-raspberry-pi-camera-1-meter.html
Raspberry Pi 3 Model B+ | 1 | Pi Microcontroller | Core Electronics | https://core-electronics.com.au/raspberry-pi-3-model-b-plus.html
16GB MicroSD card with NOOBS for Raspberry Pi 3 Model B+ | 1 | Operating disk for Pi | Core Electronics | https://core-electronics.com.au/16gb-microsd-card-with-noobs-for-raspberry-pi-3-model-b.html
Raspberry Pi 3+ Power Supply (Official) | 1 | Power Cable for Pi | Core Electronics | https://core-electronics.com.au/raspberry-pi-3-power-supply.html
Nuts and Bolts
M2 12 PRSTMC Z100 - Machine Screw, M2, 12 mm, Steel, Bright Zinc, Pan Head Pozidriv | 24 | Connect mechanical parts | element14 | https://au.element14.com/tr-fastenings/m212-prstmcz100/screw-pozi-pan-steel-bzp-m2x12/dp/1420387
M2- HFST-Z100- - Nut, Hex, M2, Steel, Bright Zinc Plated, Pack of 100 | 24 | Connect mechanical parts | element14 | https://au.element14.com/tr-fastenings/m2-hfst-z100/full-nut-steel-bzp-m2/dp/1419445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
M3 10 PRSTMC Z100 - Machine Screw, M3, 10 mm, Steel, Bright Zinc, Pan Head Pozidriv | 10 | Connect mechanical parts | element14 | https://au.element14.com/tr-fastenings/m310-prstmcz100/screw-steel-bzp-10mm-m3-pk100/dp/1420390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
M3- HFST-Z100- - Nut, Hex, M3, Steel, Bright Zinc Plated, Pack of 100 | 10 | Connect mechanical parts | element14 | https://au.element14.com/tr-fastenings/m3-hfst-z100/nut-full-steel-bzp-m3-pk100/dp/1419447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
DM3-FASTWAZ100DIN125 - Washer, Plain, Steel, Zinc Plated, M3, 3.2mm, 7mm, Pack of 100 | 10 | Connect mechanical parts | element14 | https://au.element14.com/tr-fastenings/dm3-fastwaz100din125/plain-washer-steel-3mm-7mm/dp/2506007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
M3- N5ST-Z100- - Nut, Locking, Steel, Bright-Zinc-Plated, M3, Pack of 100 | 4 | To Lock gripper links | element14 | https://au.element14.com/tr-fastenings/m3-n5st-z100/nut-locking-steel-bzp-m3-pk100/dp/1420431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
Miscellaneous items for Raspberry Pi Interfaces
RP006 - Audio / Video Cable Assembly, High Speed, HDMI Plug, HDMI Plug, 3.3 ft, 1 m, Black | 1 | Connect for Monitor Display | element14 | https://au.element14.com/pro-signal/rp006/lead-hdmi-high-speed-1m/dp/2113608
J.Burrows Wired Optical Mouse Black | 1 | For Pi interface | Officeworks | https://www.officeworks.com.au/shop/officeworks/p/j-burrows-wired-optical-mouse-black-jbm739wmbk
J.Burrows Wired Keyboard Black | 1 | For Pi interface | Officeworks | https://www.officeworks.com.au/shop/officeworks/p/j-burrows-wired-keyboard-black-jbkb620kb

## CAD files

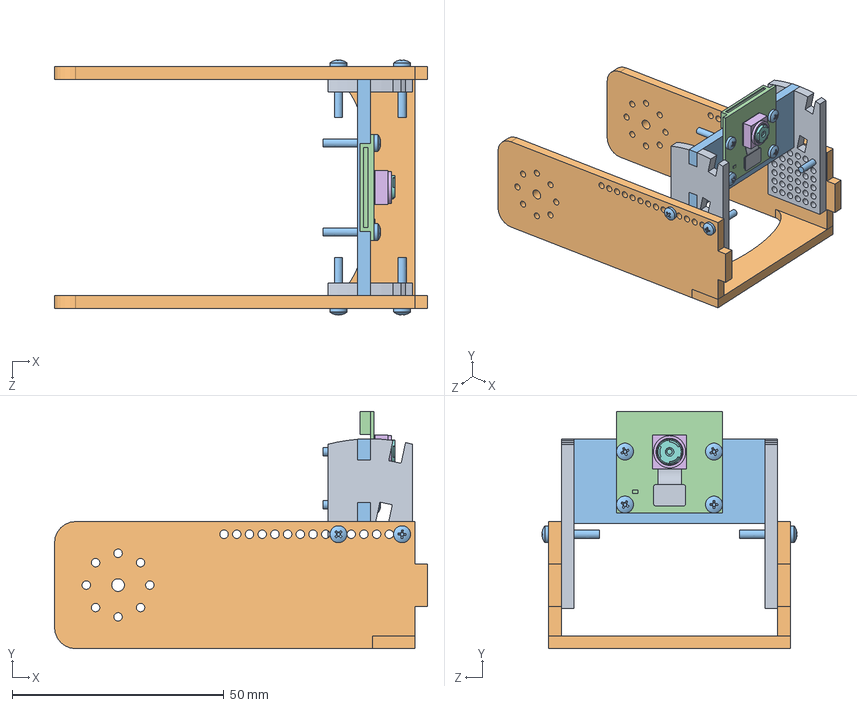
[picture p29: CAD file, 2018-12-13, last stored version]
Laser Cutting and CAD/CameraMount_Solidworks/CameraMount1.SLDASM
88.0 x 56.0 x 60.1 mm
Adjustable1 x 2
robotarmWristHoles x 2
piCameraPanel
RasPi_Camera_Board
OVA5647
OVA5647_Housing
OVA5647_IR-Glas
OVA5647_Lens
OVA5647_Pigtail
Bracing
pan cross head screw_as x 8

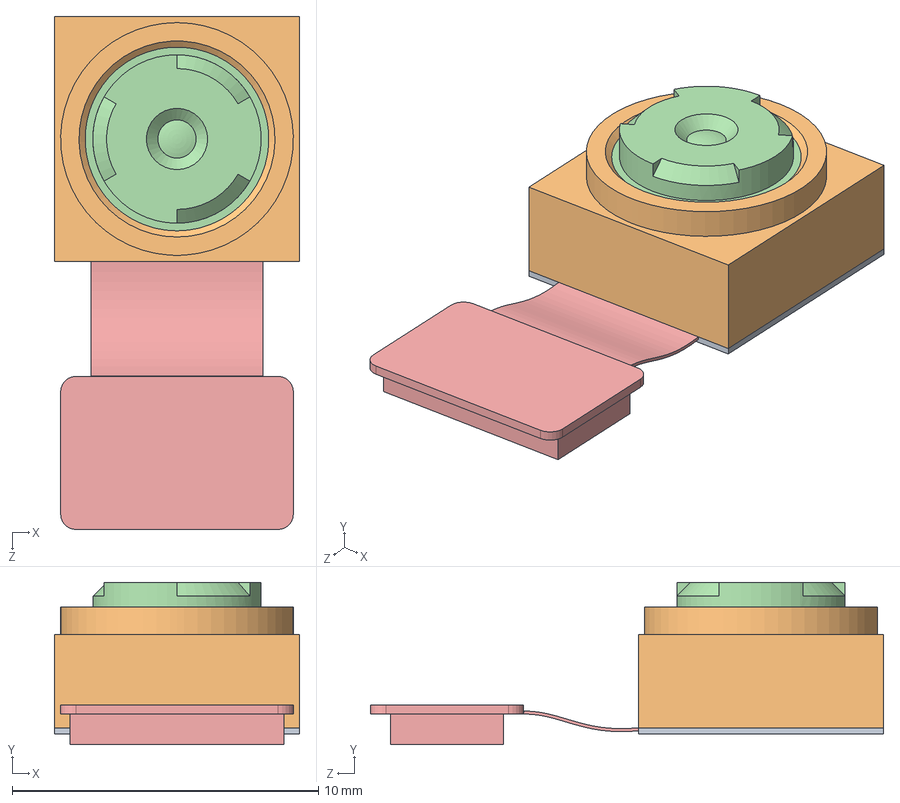
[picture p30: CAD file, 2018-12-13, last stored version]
Laser Cutting and CAD/CameraMount_Solidworks/PiCamera Solidworks/OVA5647.SLDASM
8.00 x 5.30 x 16.8 mm
OVA5647
OVA5647_Housing
OVA5647_IR-Glas
OVA5647_Lens
OVA5647_Pigtail

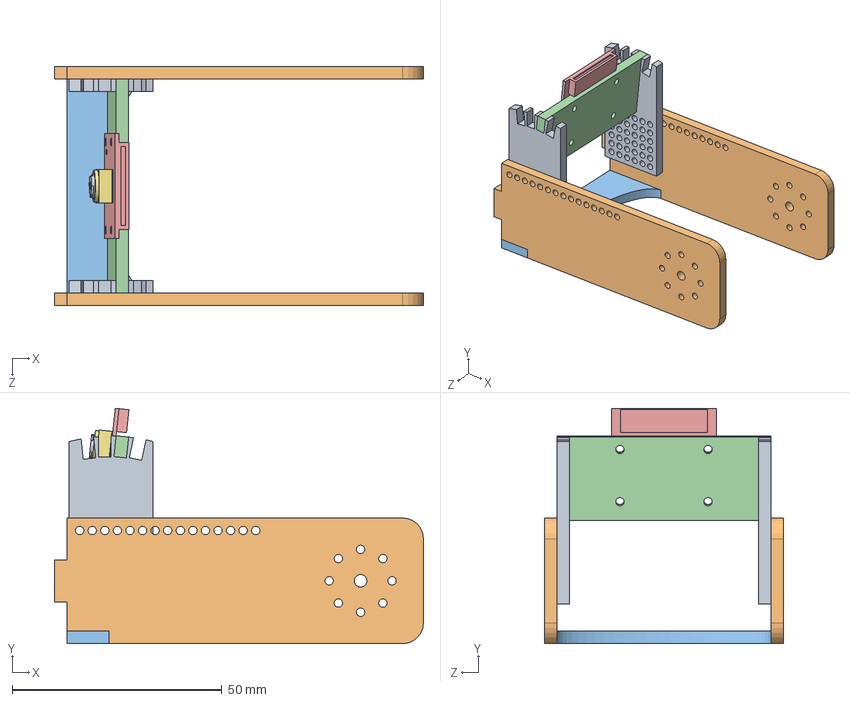
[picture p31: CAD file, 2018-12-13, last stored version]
Laser Cutting and CAD/CameraMount_Solidworks/PiCamera Solidworks/Assem1.SLDASM
88.0 x 56.2 x 57.0 mm
Adjustable1 x 2
robotarmWristHoles x 2
Bracing
piCameraPanel
RasPi_Camera_Board
OVA5647
OVA5647_Housing
OVA5647_IR-Glas
OVA5647_Lens
OVA5647_Pigtail

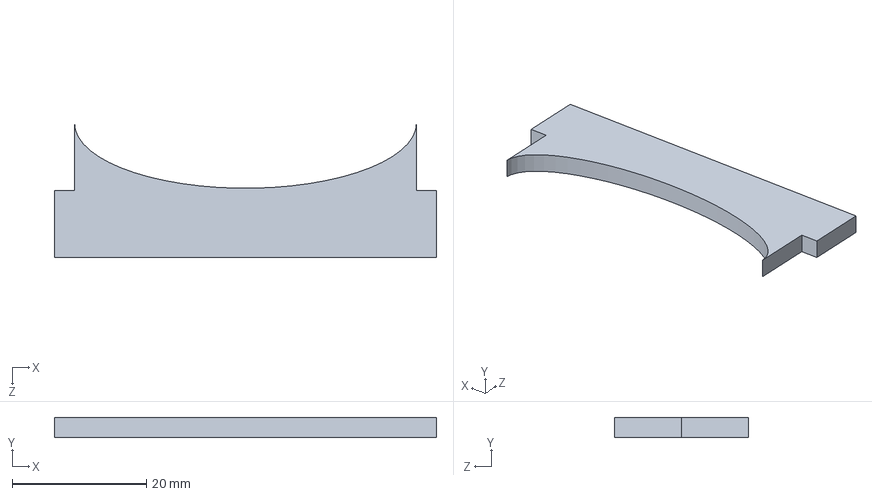
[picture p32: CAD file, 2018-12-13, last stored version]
Laser Cutting and CAD/CameraMount_Solidworks/Bracing.SLDPRT
57.0 x 3.00 x 20.0 mm

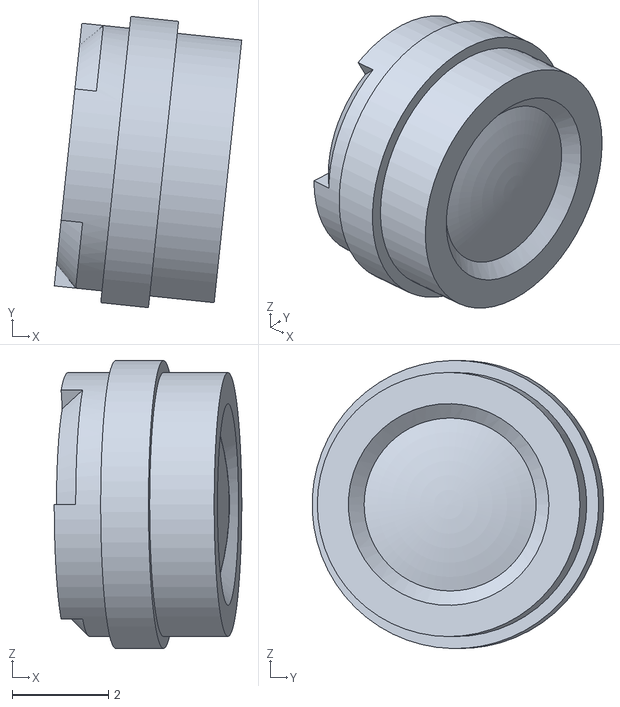
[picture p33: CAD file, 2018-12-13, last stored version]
Laser Cutting and CAD/CameraMount_Solidworks/PiCamera Solidworks/Assem1 - RasPi_Camera-1 OVA5647-2 OVA5647_Lens-1.STL
3.91 x 6.07 x 6.00

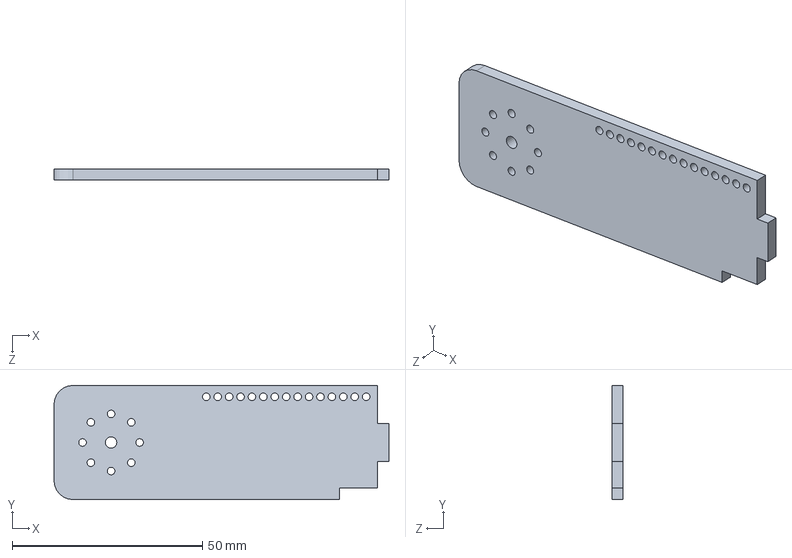
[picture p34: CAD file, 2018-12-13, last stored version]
Laser Cutting and CAD/CameraMount_Solidworks/robotarmWristHoles.SLDPRT
88.0 x 30.0 x 3.00 mm

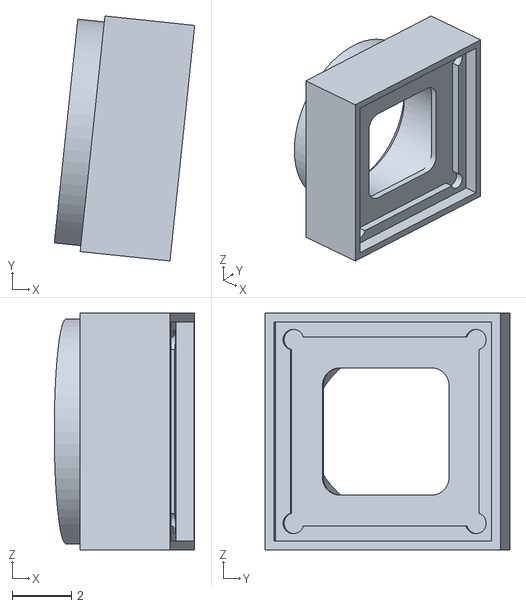
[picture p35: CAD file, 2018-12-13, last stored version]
Laser Cutting and CAD/CameraMount_Solidworks/PiCamera Solidworks/Assem1 - RasPi_Camera-1 OVA5647-2 OVA5647_Housing-1.STL
4.74 x 8.27 x 8.00

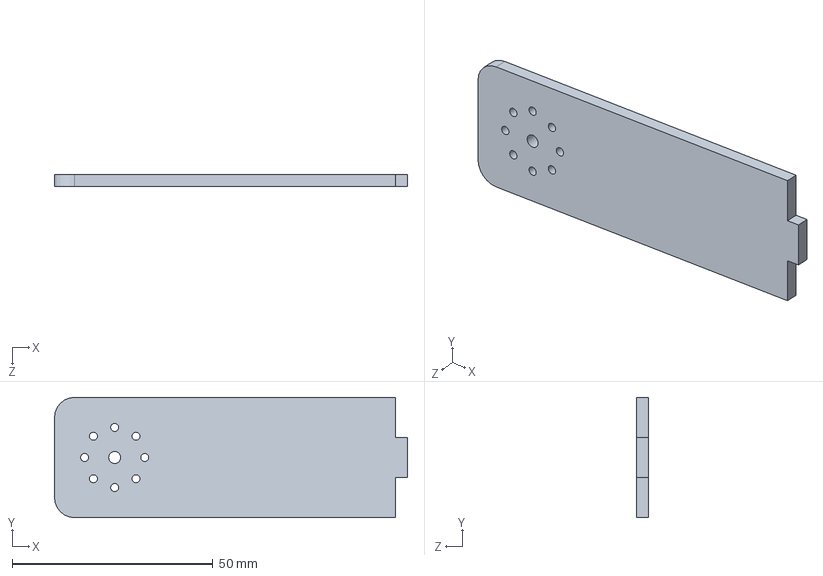
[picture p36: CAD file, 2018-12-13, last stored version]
Laser Cutting and CAD/CameraMount_Solidworks/robotarmWrist1.SLDPRT
88.0 x 30.0 x 3.00 mm

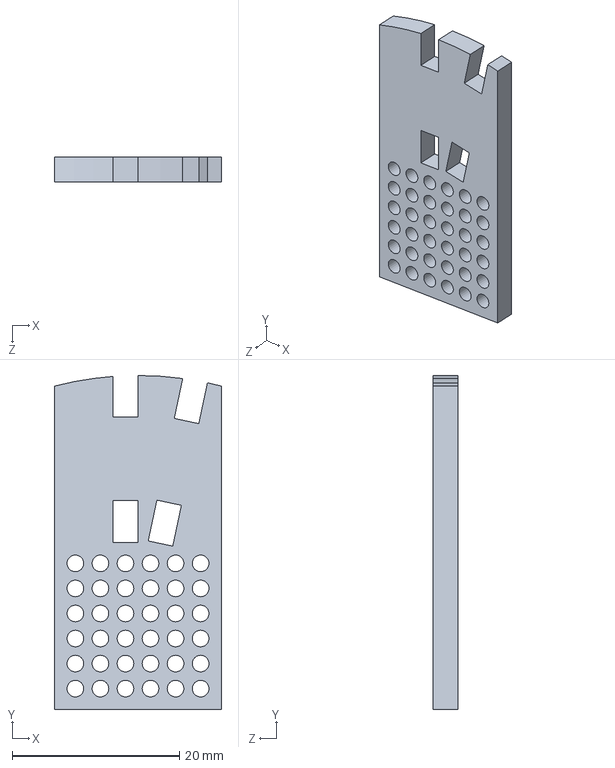
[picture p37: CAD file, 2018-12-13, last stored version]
Laser Cutting and CAD/CameraMount_Solidworks/Adjustable1.SLDPRT
20.0 x 40.0 x 3.00 mm

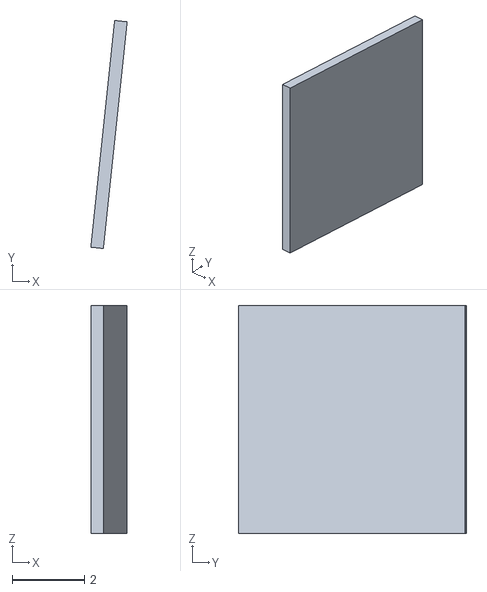
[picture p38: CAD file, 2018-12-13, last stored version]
Laser Cutting and CAD/CameraMount_Solidworks/PiCamera Solidworks/Assem1 - RasPi_Camera-1 OVA5647-2 OVA5647_IR-Glas-1.STL
1.01 x 6.30 x 6.30

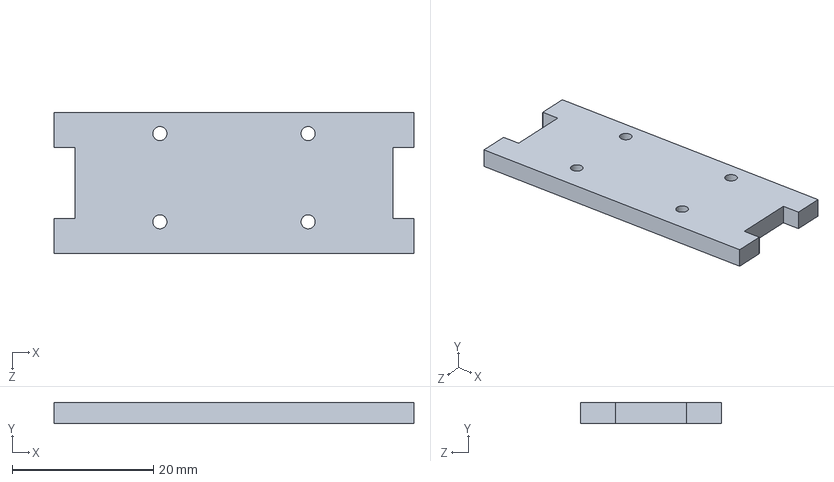
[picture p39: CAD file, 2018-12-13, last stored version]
Laser Cutting and CAD/CameraMount_Solidworks/piCameraPanel.SLDPRT
51.0 x 3.00 x 20.0 mm

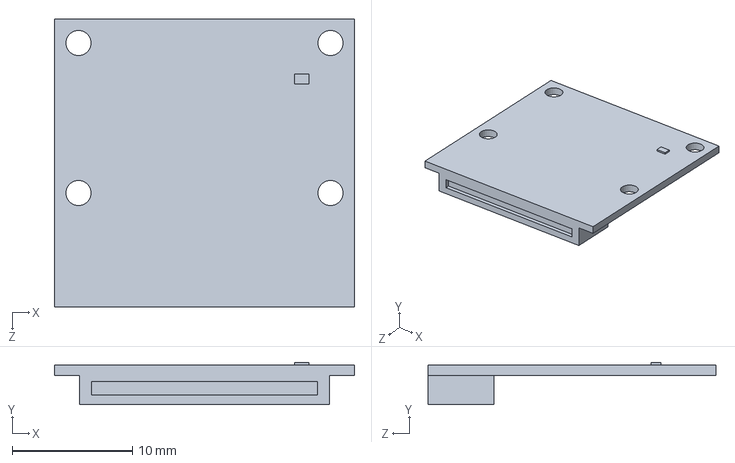
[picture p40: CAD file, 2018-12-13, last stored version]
Laser Cutting and CAD/CameraMount_Solidworks/PiCamera Solidworks/RasPi_Camera_Board.SLDPRT
25.0 x 3.50 x 24.0 mm

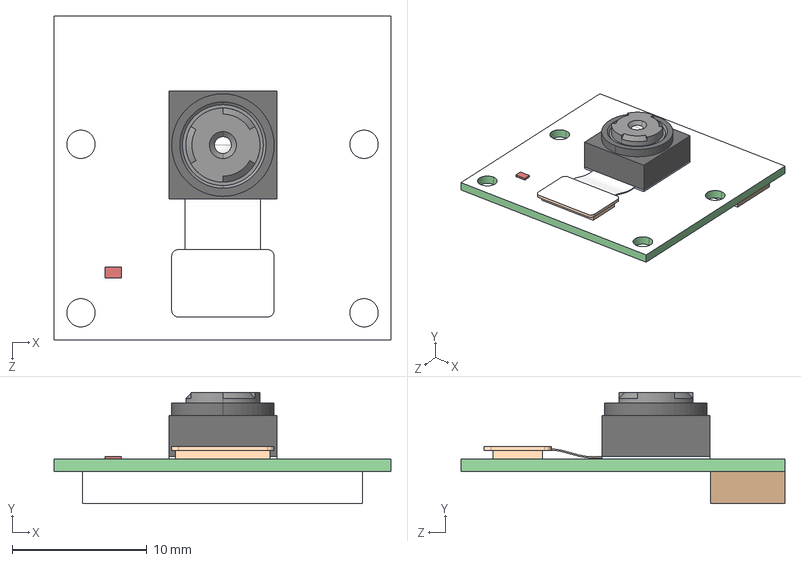
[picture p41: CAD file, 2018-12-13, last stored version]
Laser Cutting and CAD/CameraMount_Solidworks/PiCamera Solidworks/RasPi_Camera.STEP
25.0 x 8.25 x 24.0 mm
RasPi_Camera_Board_Standard
OVA5647_Standard
OVA5647_Housing_Standard
OVA5647_IR-Glas_Standard
OVA5647_Lens_FOV
OVA5647_Pigtail_Standard

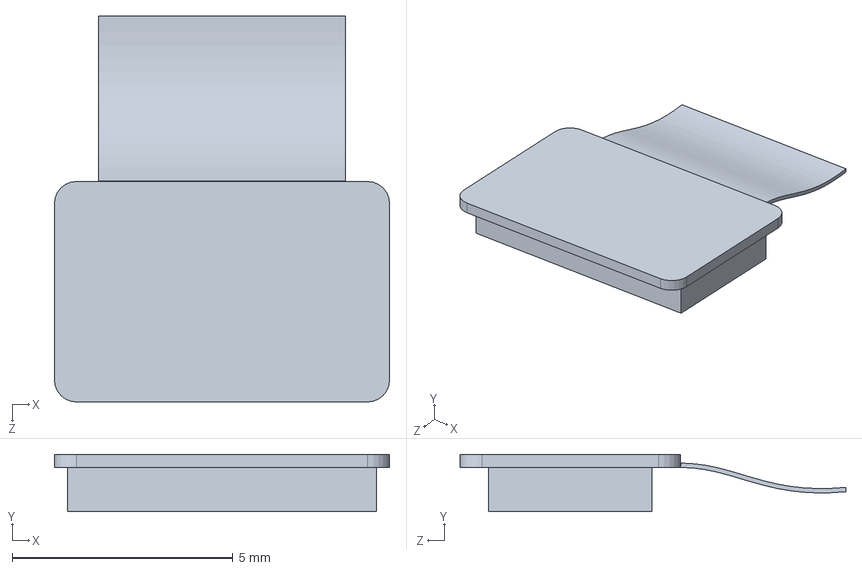
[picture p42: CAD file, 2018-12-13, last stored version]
Laser Cutting and CAD/CameraMount_Solidworks/PiCamera Solidworks/OVA5647_Pigtail.SLDPRT
7.60 x 1.30 x 8.75 mm

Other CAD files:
Laser Cutting and CAD/CameraMount_Solidworks/PiCamera Solidworks/Assem1 - Bracing-1.STL
Laser Cutting and CAD/CameraMount_Solidworks/PiCamera Solidworks/Assem1 - Adjustable1-2.STL
Laser Cutting and CAD/CameraMount_Solidworks/PiCamera Solidworks/OVA5647_Lens.SLDPRT
Laser Cutting and CAD/CameraMount_Solidworks/PiCamera Solidworks/Assem1 - RasPi_Camera-1 OVA5647-2 OVA5647_Pigtail-1.STL
Laser Cutting and CAD/CameraMount_Solidworks/PiCamera Solidworks/Assem1 - Adjustable1-1.STL
Laser Cutting and CAD/CameraMount_Solidworks/PiCamera Solidworks/Assem1 - RasPi_Camera-1 OVA5647-2 OVA5647-1.STL
Laser Cutting and CAD/CameraMount_Solidworks/PiCamera Solidworks/Assem1 - RasPi_Camera-1 RasPi_Camera_Board-1.STL
Laser Cutting and CAD/CameraMount_Solidworks/PiCamera Solidworks/Assem1 - piCameraPanel-1.STL
Laser Cutting and CAD/CameraMount_Solidworks/PiCamera Solidworks/Assem1 - robotarmWristHoles-1.STL
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

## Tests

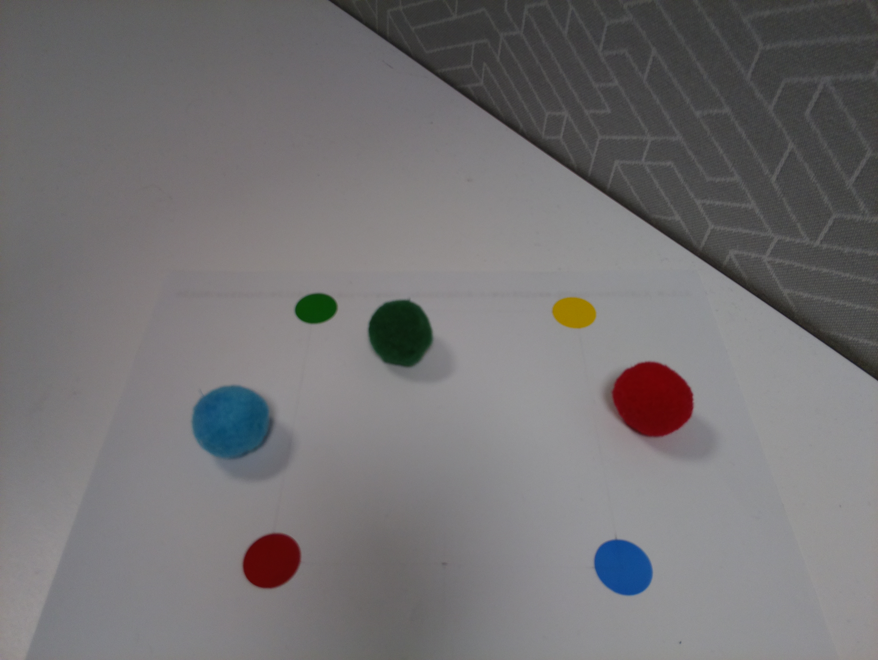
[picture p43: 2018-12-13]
Computer_vision_Workshops/opencv_prac/test.jpg

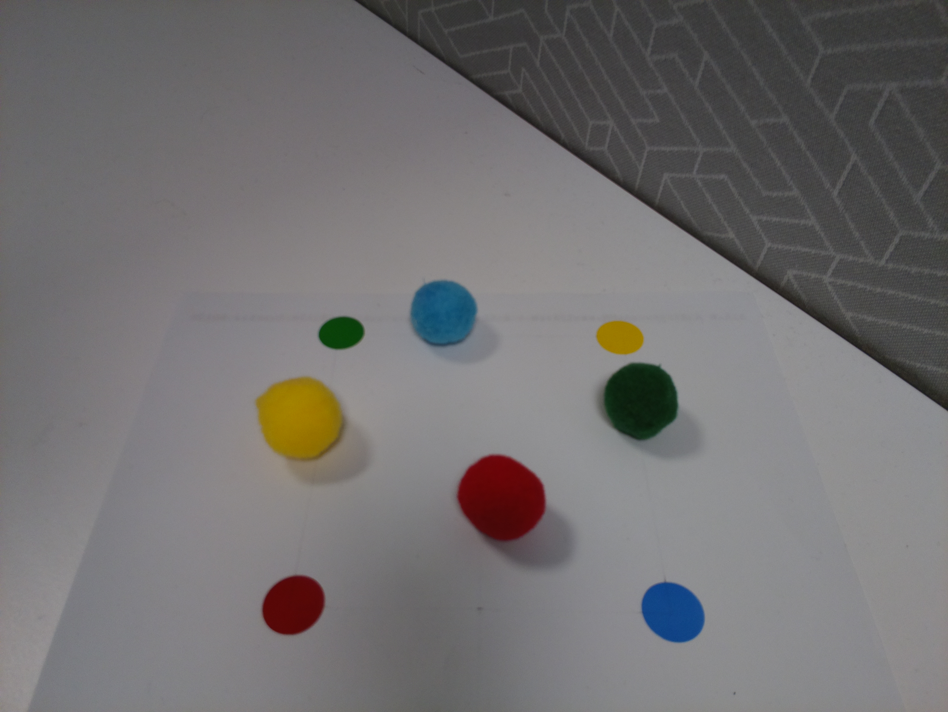
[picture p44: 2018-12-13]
Computer_vision_Workshops/opencv_prac/test1.jpg

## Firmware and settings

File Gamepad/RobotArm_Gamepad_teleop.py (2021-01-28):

#!usr/bin/env python
"""
Robot arm Control Script with Gamepad to find the event number type
command  ls /dev/input into terminal
Script to control the Workshop arms so that they go to a point
Created for Semester 1 workshops 2018
@author: Andrew Razjigaev President of QUT Robotics Club
"""

import smbus, numpy, time

from evdev import InputDevice, categorize, ecodes

from math import sin, cos, pi

from RobotarmServo_module import pi_servo, initialise_piHat

from RobotarmKinematics_module import update_joints, WorkspaceBoundaryCheck, measure_position_error, DH_matrix, ForwardKinematics, compute_error, compute_Jacobian, damped_least_squares

from RobotarmGamePadUtility_module import read_gamepad, move_arm, Move_arm_to_home, Reset_robot_arm, read_arm, Initialise_Robot_arm, robotarmLimits


# ***** MAIN ***** #
if __name__ == "__main__":

    print('STARTING ROBOT ARM...')
    
    ####INITIALISATION####
    #Initialise the Pi hat
    bus = smbus.SMBus(1) # the chip is on bus 1 of the available I2C buses
    addr = 0x40  # I2C address of the PWM chip.
    initialise_piHat()
    
    #Initialises the whole robot arm
    (m1,m2,m3,m4,m5) = Initialise_Robot_arm(bus)

    #set pwmValues for gripper:
    closed_grip_value = 500 #410
    open_grip_value = 900
    
    #Start arm at home position
    Move_arm_to_home(m1,m2,m3,m4,m5,closed_grip_value,bus)

    ####DEFINITIONS####
    #Measure arm segments l1,l2,l3,l4
    arm_lengths = (100,120,140,140)

    #Determine initial position set the desired pose there
    joint_values = read_arm(m1,m2,m3,m4)
    #initial conditions (0.0, 135.0, -100.0, -90.0)

    #Speed limit for velocity control:
    speedlimit = 10 # mm per dt

    #Set Initial target to be its starting point
    Desired_pose = ForwardKinematics(joint_values,arm_lengths)

    #While loop for the control
    on = True
    reset = False
    #set gripper to initially be closed
    grip_value = closed_grip_value

    ###Initialise the GAMEPAD CONTROL and MAPPING:
    gamepad = InputDevice('/dev/input/event3')
    #To find what event your device is use command in terminal:
    # ls /dev/input

    #Game button hold initialisation:
    hold = (0,0,0,0)
    
    print('Running loop ... Press Gamepad buttons now')
    
    ####CONTROL LOOP####
    #Run loop to follow the desired pose updated by the gamepad
    while(on):

        #Compute the Current tool point Location
        tool_point = ForwardKinematics(joint_values,arm_lengths)

        #Read the gamepad presses and compute the new pose and gripper and
        #whether the user killed the robot
        (Desired_pose,grip_value,on,reset,hold) = read_gamepad(gamepad,Desired_pose,grip_value,on,closed_grip_value,open_grip_value,reset,hold)

        #Reset robot to initial position and move desired pose back to start, gripper closed
        if reset==True:
            print('Resetting...')           
            Reset_robot_arm(m1,m2,m3,m4,m5,closed_grip_value,bus)
            joint_values = read_arm(m1,m2,m3,m4)
            Desired_pose = ForwardKinematics(joint_values,arm_lengths)
            grip_value = closed_grip_value
            reset = False

        #Check if the tool_point is within 2mm to the desired pose:
        if measure_position_error(Desired_pose,tool_point)>2:
            
            #Keep moving to target
            #compute the error vector and normalise it to the speed limit
            dX = compute_error(Desired_pose,tool_point,speedlimit)

            #compute the Jacobian / derivative of tool and joint
            J = compute_Jacobian(joint_values,arm_lengths)

            #Retrieve Joint Limits
            (joint_mins, joint_maxs) = robotarmLimits(m1,m2,m3,m4)
            
            #Compute the inverse Jacobian 
            inv_J = damped_least_squares(J, joint_values, joint_mins, joint_maxs)
            
            #Estimate the required joint update to reduce positon error
            dQ = numpy.dot(inv_J,dX)

            #update the joints
            new_joint_values = update_joints(joint_values,dQ)

            #Check if update is consistent with workspace:
            if WorkspaceBoundaryCheck(joint_values, new_joint_values, joint_mins, joint_maxs) is True:
                #Keep the user input inside workspace by setting it is the current tool point:
                Desired_pose = tool_point

            #Move the robot arm
            move_arm(new_joint_values,grip_value,m1,m2,m3,m4,m5,bus)

            #Read the current joint angles
            joint_values = read_arm(m1,m2,m3,m4)

        else:
            #Update only gripper
            #Move the robot arm
            move_arm(joint_values,grip_value,m1,m2,m3,m4,m5,bus)


    #END STATE    
    #When the user kills the while loop, reset the robot and turn off
    print('TERMINATING ROBOT ARM')
    Reset_robot_arm(m1,m2,m3,m4,m5,closed_grip_value,bus)
    print('ROBOT ARM PROGRAM HAS ENDED')

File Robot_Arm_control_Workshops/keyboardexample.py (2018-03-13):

import time

import getch
'''
thanks to:
https://pypi.python.org/pypi/getch#downloads

but can only run in the terminal type
python3 keyboardexample.py
'''
x = 0
y = 0
z = 0
p = 0


while True:
    
    ch = getch.getch()
    
    if ch == 'a':
        x = x + 5
    elif ch == 's':
        y = y - 5
    elif ch == 'd':
        x = x - 5
    elif ch == 'w':
        y = y + 5

    print('x = '+str(x)+' y = '+str(y))
        
        

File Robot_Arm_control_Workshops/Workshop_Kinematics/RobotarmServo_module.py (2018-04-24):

"""
Robot arm Servo class Module
Based on the Sparkfun Raspberry Pi Servo Hat in Example.py
Created for Semester 1 workshops 2018
@author: Andrew Razjigaev President of QUT Robotics Club
    
REFERENCE:
https://learn.sparkfun.com/tutorials/pi-servo-hat-hookup-guide   
    
First point: in most OS level interactions, the I2C communication bus is 
referred to as SMBus. Thus we get our first lines of code. 
This imports the smbus module, creates an object of type SMBus, and attaches it 
to bus “1” of the Pi’s various SMBuses. We also need time and math for later 
use
We have to tell the program the part’s address. By default, it is 0x40, so set 
a variable to that for later use as well.
"""
import smbus, time, math
bus = smbus.SMBus(1) # the chip is on bus 1 of the available I2C buses

addr = 0x40  # I2C address of the PWM chip.
'''
Next, we want to enable the PWM chip and tell it to automatically increment 
addresses after a write (that lets us do single-operation multi-byte writes).
'''
def initialise_piHat():
    #initialise The I2C pi hat
    bus.write_byte_data(addr, 0, 0x20)     # enable the chip
    bus.write_byte_data(addr, 0xfe, 0x1e)  # configure the chip for multi-byte write  
      

class pi_servo:
    """
    This is a Class for the servo motors on the Sparkfun Raspberry PI servo hat
    it has a simpler function to initialise the servo
    it has a calibration function that helps map PWM signals to degrees
    it has a function to move the arm to a degree or a radian
    it has a function to track the last PWM thus angle input to the arm
    """
    
    dt = 0.01 # seconds for motor update
    
    #FUNCTION ASSIGNS START AND STOP ADDRESSES AUTOMATICALLY
    #By incrementing the value by 4
    def _init_channel(self,channel_number):
            self.channel = 0 + channel_number
            self.start = 0x06 + 4*channel_number
            self.stop = 0x08 + 4*channel_number

    #functions to turn on and turn off the motor
    def fstart(self,bus):
        bus.write_word_data(addr, self.start, 0) 

    def fstop(self,bus):
        bus.write_word_data(addr, self.stop, 0)
           
    #Calibration Variables for the Joint Limit
    def _calibrate_servo(self,min_deg,mid_deg,max_deg):
        '''
        Test the servos before hand with values 836 and 1664
        measure their corresponding values 
        check PWM 1250 and see if you get and angle in between them.
        '''
        #Define two limits for the working region 
        self.max_limit = max_deg
        self.neutral = mid_deg
        self.min_limit = min_deg
        #They relate to the PWMs 1664, 1250 and 836
        self.max_PWM = 1664 # 2.0ms
        self.mid_PWM = 1250 # Neutral 1.5ms
        self.min_PWM = 836 # 1 ms  

    #JOINT LIMIT DEFINITION FUNCTION
    def define_jointlimits(self,minimum,maximum):
        '''
        You can define you're own minimum and maximum joint limits here based 
        on measuring the output angle in degrees with your PWM signals
        '''
        self.absolute_min = minimum
        self.absolute_max = maximum
        

    '''
    MAPPING DEGREES TO PWM
    '''
    def deg2PWM(self,deg):
       
        #Linear relationship constants
        m = (self.max_PWM - self.min_PWM)/(self.max_limit - self.min_limit)
        c = self.max_PWM - m*(self.max_limit)

        #JOINT LIMIT LOGIC
        if m < 0:  #m is negative gradient
            #the difference is to reverse our interpretation
            #of max limit and min limit because of the gradient
            if deg>self.absolute_min:
                #upper Limit
                angle = self.absolute_min 
            elif deg<self.absolute_max:
                #lower limit
                angle = self.absolute_max
            else:
                angle = deg

        else: #m is positive gradient default
            if deg<self.absolute_min:
                #lower Limit
                angle = self.absolute_min
            elif deg>self.absolute_max:
                #Upper limit
                angle = self.absolute_max
            else:
                angle = deg
                
        #Linear relationship mapping angle to PWM    
        PWM = m*angle + c        

        #Record the inverse mapping to read the actual angle input
        self.last_deg = (PWM - c)/m

        #give the pwm signal corresponding to the angle
        return PWM

    '''
    OUTPUT FUNCTIONS FOR MOVING THE SERVOS
    '''
    def move_pwm(self,pwm,bus):
        #always round just in case, get integer
        PWM = int(round(pwm))
        
        #Gives a pwm signal to the bus
        bus.write_word_data(addr, self.stop, PWM) 
        
        #RECORD THE PWM OUTPUT
        self.last_pwm = PWM
        
        #Do inverse mapping to find the angle that PWM gave
        m = (self.max_PWM - self.min_PWM)/(self.max_limit - self.min_limit)
        c = self.max_PWM - m*(self.max_limit)
        
        #RECORD THE ANGLE OUTPUT
        self.last_deg = (PWM - c)/m

        #Give the controller some time to move
        #time.sleep(self.dt)   
        
        

    def move_deg(self,degrees,bus):
        #Gives a pwm signal to the bus based on a degree input
        PWM_val = self.deg2PWM(degrees)
        #Output that PWM
        self.move_pwm(round(PWM_val),bus)



    def move_rad(self,radians,bus):
        #Gives a pwm signal to the bus based on a radians input
        #Convert radians to degrees
        degrees = radians*(180/math.pi)
        #compute PWM
        PWM_val = self.deg2PWM(degrees)
        #Output that PWM
        self.move_pwm(round(PWM_val),bus)
        
    '''
    READING OUTPUT FUNCTIONS FOR TRACKING JOINT ANGLE
    '''
    def read_pwm(self):
        #Returns the last given pwm
        return self.last_pwm

    def read_deg(self):
        #Returns the last given degree
        return self.last_deg

    def read_rad(self):
        #Returns the last given radian
        radian = self.last_deg*(math.pi/180) 
        return radian        

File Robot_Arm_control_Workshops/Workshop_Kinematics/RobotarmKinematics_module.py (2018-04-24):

"""
Robot arm Kinematics Module Kinematics Workshop Version
Based on theory from Intro to Robotics
Created for Semester 1 workshops 2018
@author: Andrew Razjigaev President of QUT Robotics Club
"""
import numpy

from math import sin, cos, pi

#Kinematics Workshop Version - will get fatter in the next workshops

#TODO:
#Find the DH Parameters for Each Joint in the Forward Kinematics Function


def DH_matrix(theta,d,a,alpha):
    '''
    Computes the Homogeneous Transformation matrix A from 4 parameters:
    such that:
    A = Rz(theta)*Tz(d)*Tx(a)*Rx(alpha)    
    '''
    A = numpy.matrix([[cos(theta), -sin(theta)*cos(alpha),  sin(theta)*sin(alpha), a*cos(theta)],
                      [sin(theta),  cos(theta)*cos(alpha), -cos(theta)*sin(alpha), a*sin(theta)],
                      [0,           sin(alpha),             cos(alpha),            d],
                      [0,           0,                      0,                     1]])
    return A;
    
    
def ForwardKinematics(joint_values,arm_lengths):
    '''
    Computes the Forward Kinematics i.e. x,y,z and pitch angle of the tool 
    point given joint angles and lengths  
    '''
    q1,q2,q3,q4 = joint_values
    l1,l2,l3,l4 = arm_lengths
    
    a0 = 0 #odd offset is 0 only if rotating base z axis points 
           #to the origin of the joint 2 coordinate frame

    #ADD DH PARAMETERS IN HERE
    baseTjoint1 = DH_matrix()
    joint1Tjoint2 = DH_matrix()
    joint2Tjoint3 = DH_matrix()
    joint3Tgripper = DH_matrix()

    BT2 = numpy.dot(baseTjoint1,joint1Tjoint2)
    BT3 = numpy.dot(BT2,joint2Tjoint3)
    baseTgripper = numpy.dot(BT3,joint3Tgripper)
    
    x = baseTgripper[0,3]
    y = baseTgripper[1,3]
    z = baseTgripper[2,3]
    
    pitch = q2 + q3 + q4
    
    return (x,y,z,pitch);  

  
